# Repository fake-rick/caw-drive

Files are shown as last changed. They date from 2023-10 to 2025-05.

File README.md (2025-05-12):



# 🐦 CawDrive - 无刷电机驱动器

---



中文 | [English](https://github.com/fake-rick/caw-drive/blob/master/Docs/README_EN.md)

# 🚀 简介

- 支持 24 电压输入

- 外部编码器接口支持：霍尔，SPI，I2C

- 主控芯片：STM32F446，电机驱动芯片为 DRV8323RSRGZR

- 板载磁编码器：MT6835GT-STD（21bit）

- 支持电机线圈温度采样和驱动器温度采样

- 支持双路低端相电流采样

- 支持母线电压采样

- 支持CAN和USART通讯

- 支持SWD下载和调试

- 支持 6xPWM 和 3xPWM 的控制

# 🗂️ 目录

* Firmware：旧版代码（弃用）

* Firmware_F446：FOC控制的实际控制代码以及STM32CubeMX配置

* PCB：FOC驱动器原理图、PCB以及生成的Gerber文件

# 📦 固件编译（开发中）

## 配置caw-embedded库

当前固件编译依赖caw-embedded项目: https://github.com/fake-rick/caw-embedded

依赖添加方式1：

可以直接将caw-embedded项目克隆到caw-drive/Firmware目录下:

```bash
cd caw-drive/Firmware
git clone git@github.com:fake-rick/caw-embedded.git caw_embedded
```

依赖添加方式2：

将caw-embedded项目克隆后建立链接（Linux），假设将caw-embedded放在与caw-drive同级目录下:

```bash
git clone git@github.com:fake-rick/caw-embedded.git
cd caw-drive/Firmware
ln -s ../../caw-embedded caw_embedded
```

# 🛠 VSCode配置

安装并配置stm32-for-vscode插件

# 👻 图片展示

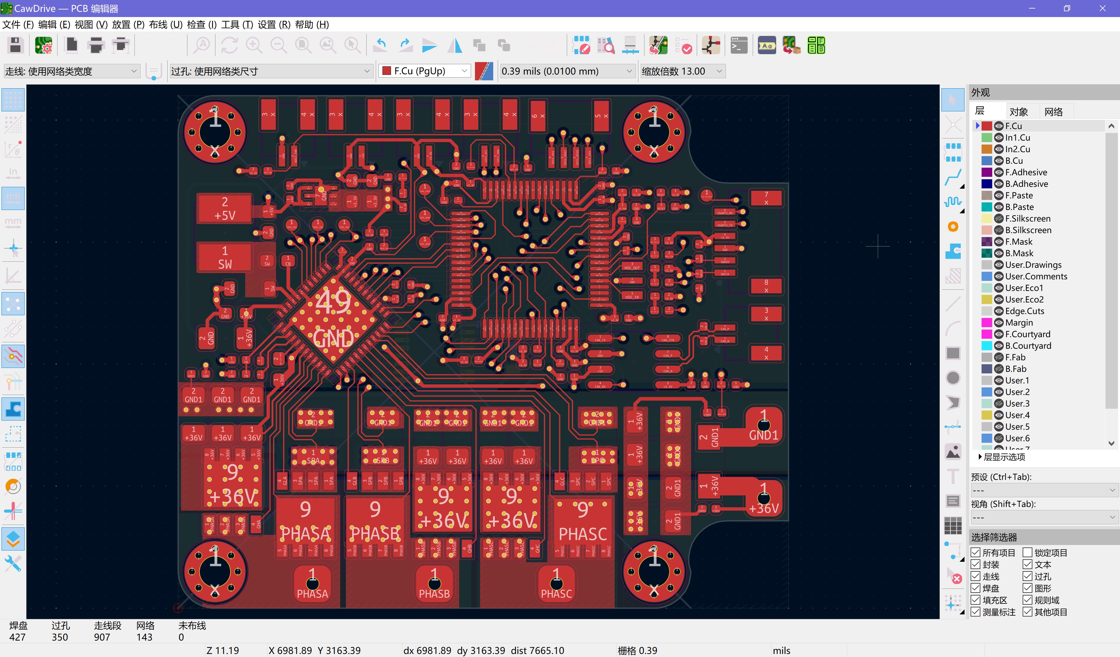
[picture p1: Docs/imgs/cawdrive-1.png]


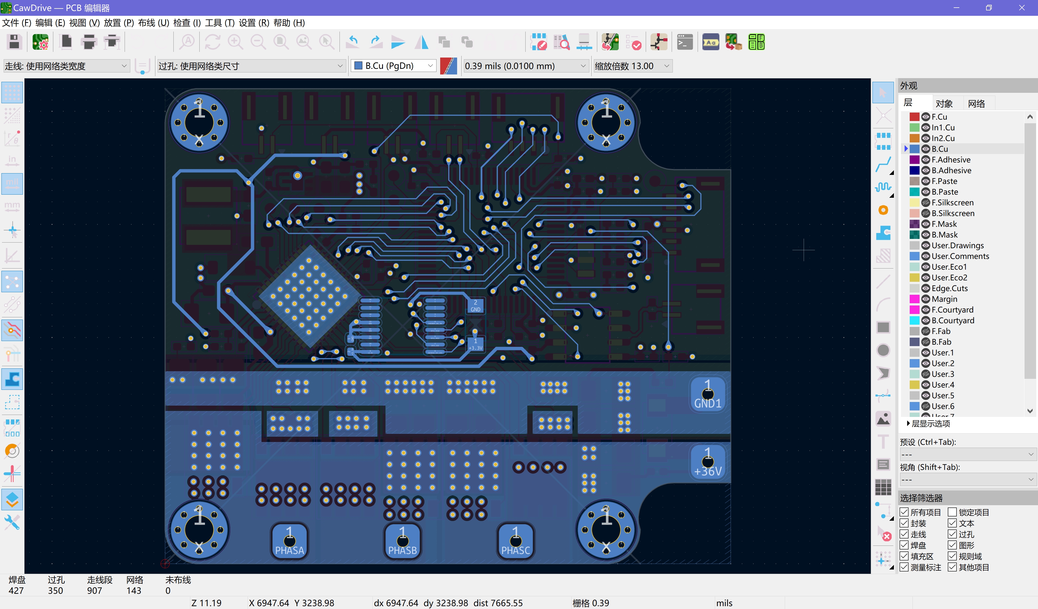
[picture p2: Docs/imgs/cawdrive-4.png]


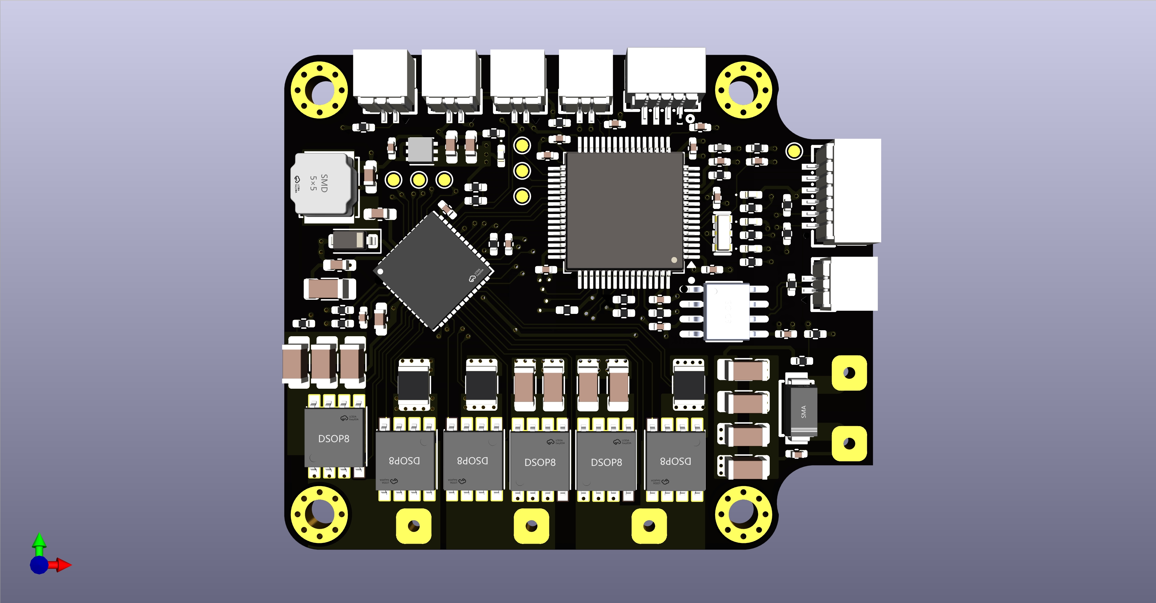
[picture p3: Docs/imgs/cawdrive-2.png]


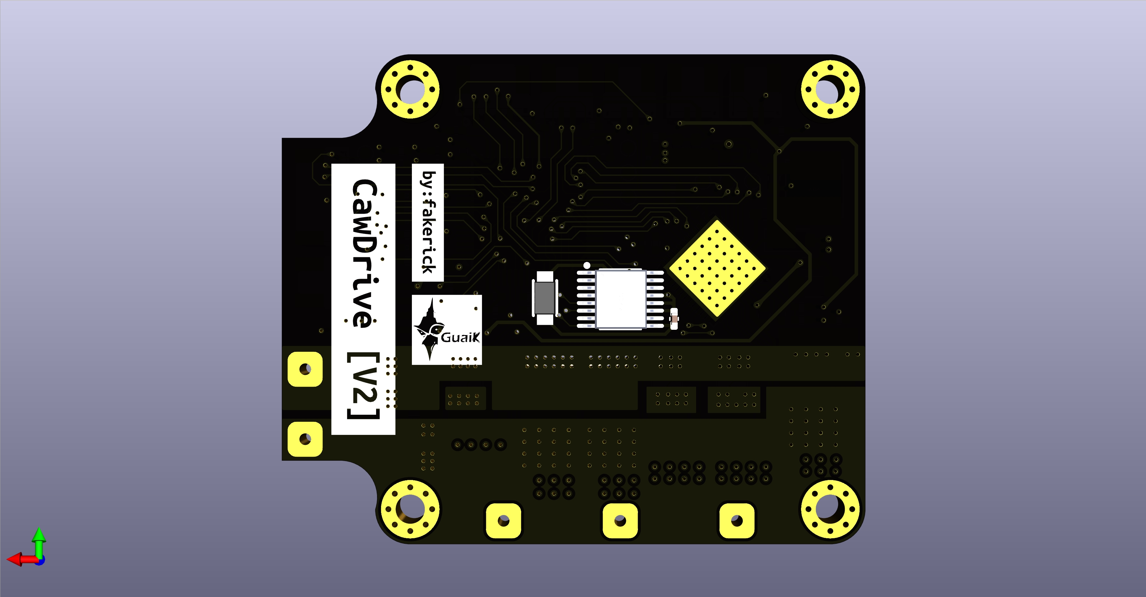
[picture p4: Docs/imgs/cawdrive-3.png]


# 🖥️ 上位机

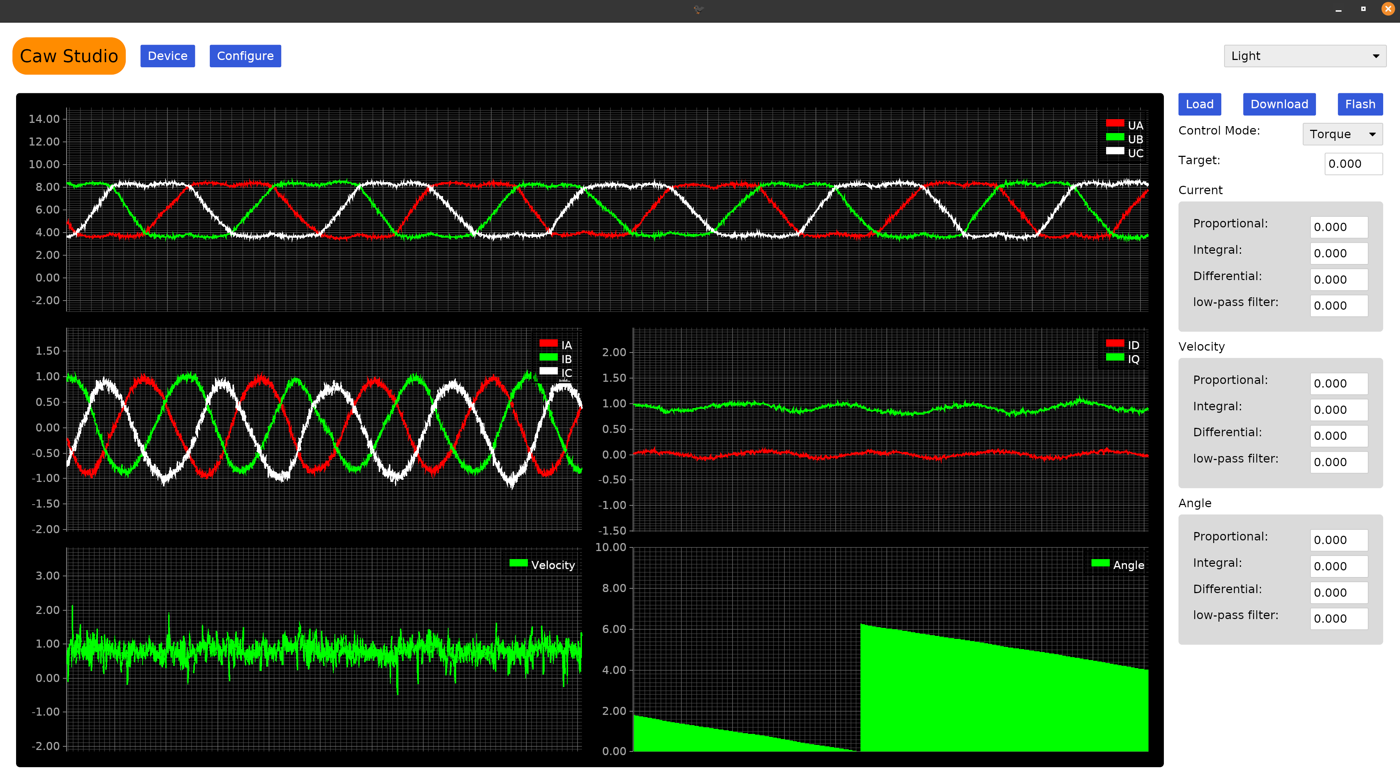
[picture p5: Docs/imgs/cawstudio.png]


# 📝 参考资料

https://github.com/bgkatz/3phase_integrated

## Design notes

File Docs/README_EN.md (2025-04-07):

# 🐦 CawDrive - Brushless Motor Driver

---



# 🚀 Introduction

- Supports 24V input

- External encoder interface support: Hall, SPI, I2C

- Main control chip: STM32F446, motor driver chip: DRV8323RSRGZR

- Onboard magnetic encoder: MT6835GT-STD (21-bit)

- Supports motor coil temperature sampling and driver temperature sampling

- Supports 3-phase low-side current sampling

- Supports bus voltage sampling

- Supports CAN and USART communication

- Supports SWD download and debugging

- Supports 6xPWM and 3xPWM control

# 🗂️ Directory

* Firmware: Legacy code (deprecated)

* Firmware_F446: Actual control code for FOC control and STM32CubeMX configuration

* PCB: FOC driver schematics, PCB, and generated Gerber files

# 📦 Firmware Compilation (Under Development)

## Configure the caw-embedded Library

The current firmware compilation depends on the caw-embedded project: https://github.com/fake-rick/caw-embedded

Dependency Addition Method 1:

You can directly clone the caw-embedded project into the `caw-drive/Firmware` directory:

```bash
cd caw-drive/Firmware
git clone git@github.com:fake-rick/caw-embedded.git caw_embedded
```

Dependency Addition Method 2:

Clone the caw-embedded project and create a symbolic link (Linux). Assuming the caw-embedded project is placed in the same level directory as caw-drive:

```bash
git clone git@github.com:fake-rick/caw-embedded.git
cd caw-drive/Firmware
ln -s ../../caw-embedded caw_embedded
```

# 🛠 VSCode Configuration

Install and configure the stm32-for-vscode plugin

# 👻 Image Showcase







# 🖥️ Upper Computer



# 📝 References

https://github.com/bgkatz/3phase_integrated

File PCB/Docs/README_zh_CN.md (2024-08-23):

# CawDrive - 无刷电机驱动器

---



# 🚀 简介

- 支持 24 电压输入

- 当前版本支持 SPI，串口和 CAN FD 总线通讯，支持 TIM PWM 刹车功能

- 主控芯片：STM32G474，电机驱动芯片为 DRV8323RSRGZR

- 板载磁编码器：AS5047P

- 支持一路NTC采样

- 支持 6xPWM 和 3xPWM 的控制

# ☕ 支持

### 💰 微信 & 支付宝：

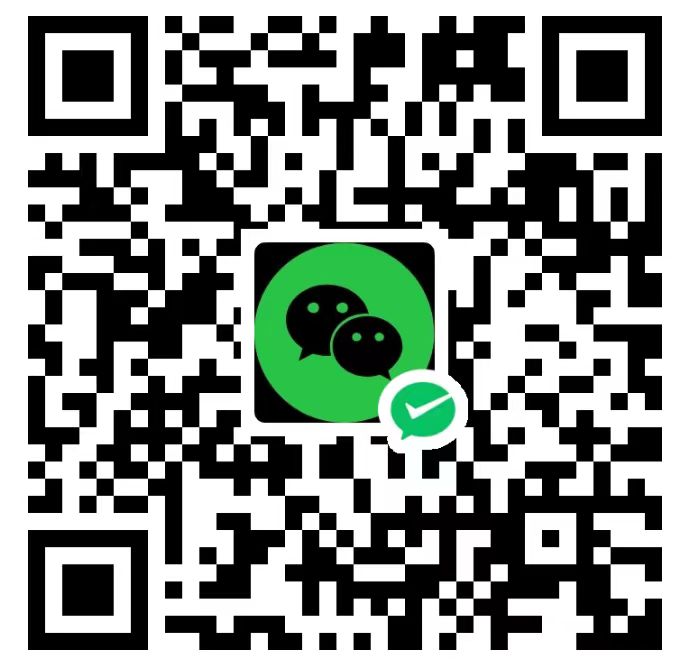
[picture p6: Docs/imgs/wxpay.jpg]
https://github.com/fake-rick/caw-drive/blob/master/Docs/imgs/wxpay.jpg?raw=true
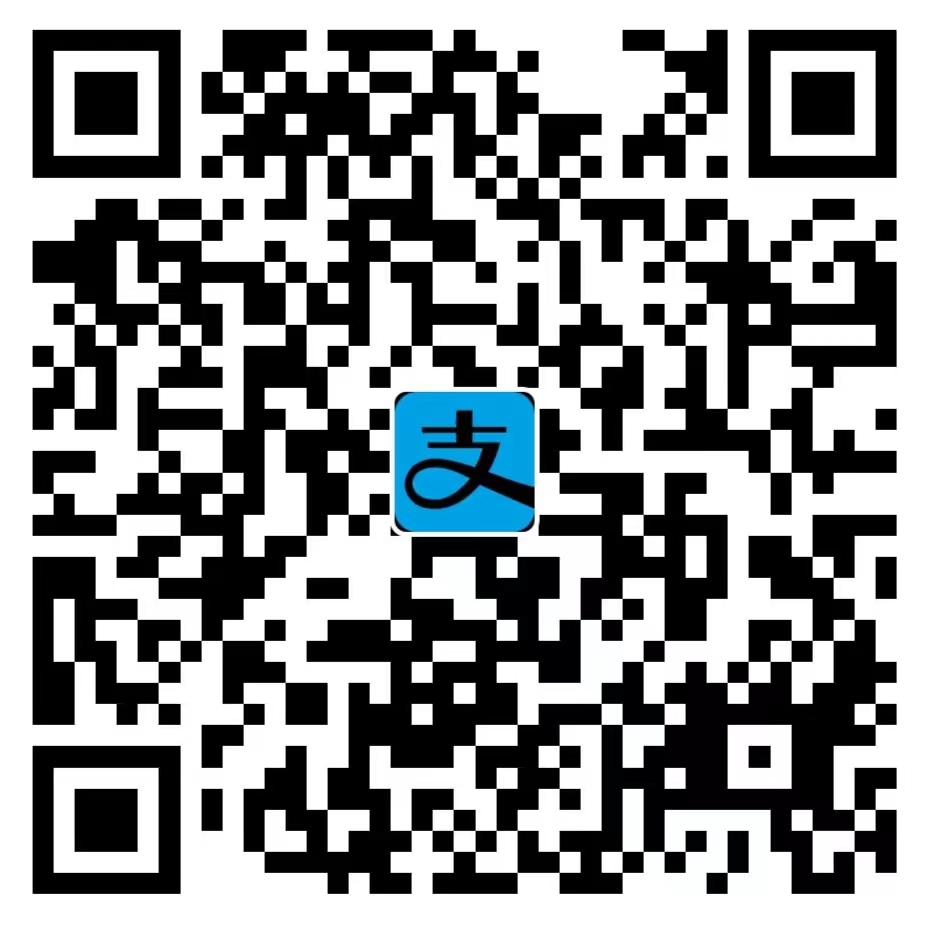
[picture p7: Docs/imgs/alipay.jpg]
https://github.com/fake-rick/caw-drive/blob/master/Docs/imgs/alipay.jpg?raw=true
 

# 📝 参考资料

[bgkatz/3phase_integrated: 3-phase motor controller with integrated position sensor (github.com)](https://github.com/bgkatz/3phase_integrated)

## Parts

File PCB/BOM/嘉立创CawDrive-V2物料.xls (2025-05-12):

购买类型 | 商品编号 | 物料编码 | 商品分类 | 名称 | 商品型号 | 品牌 | 封装规格 | 单个毛重 | 购买数量 | 商品单价(元) | 金额(元)
现货 | C87270 |  | 静电和浪涌保护(TVS/ESD) | 双向TVS 36V截止 6.9A峰值脉冲 编带 | SMAJ36CA/TR13 | Brightking(君耀电子) | SMA(DO-214AC) | 0.000122000 | 20 | 0.224 | 4.48
现货 | C3029343 |  | 线对板针座 | 1x4P 间距:1mm 卧贴 系列:SH 编带 | WAFER-SH1.0-4PWB | XUNPU(讯普) | SMD,P=1mm,卧贴 | 0.000240000 | 5 | 0.557 | 2.79
现货 | C3029345 |  | 线对板针座 | 1x6P 间距:1mm 卧贴 系列:SH 编带 | WAFER-SH1.0-6PWB | XUNPU(讯普) | SMD,P=1mm,卧贴 | 0.000270000 | 5 | 0.6758 | 3.38
现货 | C141553 |  | 场效应管(MOSFET) | 1个N沟道 耐压:40V 电流:92A 编带 | TPH3R704PL,L1Q | TOSHIBA(东芝) | DSOP-8-EP-5.0mm | 0.000107000 | 12 | 3.73 | 44.76
现货 | C69336 |  | 单片机(MCU/MPU/SOC) | MSL=3 带DSP和FPU的高性能基础系列ARM Cortex-M4 MCU，具有512 KB Flash、180 MHz CPU、ART加速器和双QSPI 托盘 | STM32F446RET6 | ST(意法半导体) | LQFP-64(10x10) | 0.001913000 | 2 | 31.65 | 63.3
现货 | C2848334 |  | 线性稳压器(LDO) | 具有可调节输出和固定输出的 1A、16V 正电压低压降 (LDO) 线性稳压器 编带 | TLV76733DRVR | TI(德州仪器) | WSON-6(2x2) | 0.000190000 | 5 | 1.2651 | 6.33
现货 | C38695 |  | CAN收发器 | TJA1051T/3/1J 编带 | TJA1051T/3/1J | NXP(恩智浦) | SOIC-8-150mil | 0.000193000 | 5 | 3.4 | 17
现货 | C3029341 |  | 线对板针座 | 1x2P 间距:1mm 卧贴 系列:SH 编带 | WAFER-SH1.0-2PWB | XUNPU(讯普) | SMD,P=1mm,卧贴 | 0.000200000 | 10 | 0.4252 | 4.25
现货 | C82544 |  | 肖特基二极管 | 电压:40V 电流:1A 编带 | 1N5819HW-7-F | DIODES(美台) | SOD-123 | 0.000035000 | 20 | 0.1823 | 3.65
现货 | C86063 |  | 贴片电感 | 39nH ±5% 编带 | LQG15HS39NJ02D | muRata(村田) | 0402 | 0.000015000 | 100 | 0.0465 | 4.65
现货 | C965790 |  | 发光二极管/LED | 停产 XL-1005SURC 编带 | XL-1005SURC | XINGLIGHT(成兴光) | 0402 | 0.000022000 | 100 | 0.0497 | 4.97
现货 | C22355736 |  | 发光二极管/LED | XL-1005UBC 编带 | XL-1005UBC | XINGLIGHT(成兴光) | 0402 | 0.000016040 | 100 | 0.0471 | 4.71
现货 | C965793 |  | 发光二极管/LED | XL-1005UGC 编带 | XL-1005UGC | XINGLIGHT(成兴光) | 0402 | 0.000022000 | 100 | 0.0478 | 4.78
现货 | C965791 |  | 发光二极管/LED | XL-1005UOC 编带 | XL-1005UOC | XINGLIGHT(成兴光) | 0402 | 0.000022000 | 50 | 0.0767 | 3.84
现货 | C167941 |  | 功率电感 | 22uH ±20% 1.2A 编带 | FNR5020S220MT | cjiang(长江微电) | SMD,5x5mm | 0.000181000 | 10 | 0.379 | 3.79
现货 | C25079 |  | 贴片电阻 | 120Ω ±1% 62.5mW 厚膜电阻 编带 | 0402WGF1200TCE | UNI-ROYAL(厚声) | 0402 | 0.000009000 | 100 | 0.0038 | 0.38
现货 | C77131 |  | NTC热敏电阻 | NCP15XH103F03RC 编带 | NCP15XH103F03RC | muRata(村田) | 0402 | 0.000015000 | 50 | 0.0674 | 3.37
现货 | C852841 |  | 贴片电阻 | 薄膜电阻 54.9kΩ ±0.1% 62.5mW 编带 | RT0402BRD0754K9L | YAGEO(国巨) | 0402 | 0.000009000 | 50 | 0.1335 | 6.68
现货 | C281777 |  | 贴片电阻 | 薄膜电阻 3kΩ ±0.1% 62.5mW 编带 | RT0402BRD073KL | YAGEO(国巨) | 0402 | 0.000009000 | 50 | 0.1253 | 6.27
现货 | C728563 |  | 贴片电阻 | 薄膜电阻 75kΩ ±0.1% 62.5mW 编带 | RT0402BRD0775KL | YAGEO(国巨) | 0402 | 0.000009000 | 50 | 0.1294 | 6.47
现货 | C2988648 |  | 电流采样电阻/分流器 | 5mΩ ±1% 1W 编带 | HoLLR1206-1W-5mR-1% | Milliohm(毫欧) | 1206 | 0.000032000 | 10 | 0.3007 | 3.01
现货 | C17168 |  | 贴片电阻 | 0Ω ±1% 62.5mW 厚膜电阻 编带 | 0402WGF0000TCE | UNI-ROYAL(厚声) | 0402 | 0.000009000 | 100 | 0.0033 | 0.33
现货 | C190095 |  | 贴片电阻 | 薄膜电阻 10kΩ ±0.1% 62.5mW 编带 | RT0402BRD0710KL | YAGEO(国巨) | 0402 | 0.000009000 | 50 | 0.1107 | 5.54
现货 | C25123 |  | 贴片电阻 | 510Ω ±1% 62.5mW 厚膜电阻 编带 | 0402WGF5100TCE | UNI-ROYAL(厚声) | 0402 | 0.000009000 | 100 | 0.0035 | 0.35
现货 | C25744 |  | 贴片电阻 | 10kΩ ±1% 62.5mW 厚膜电阻 编带 | 0402WGF1002TCE | UNI-ROYAL(厚声) | 0402 | 0.000010178 | 100 | 0.0034 | 0.34
现货 | C24497 |  | 贴片电容(MLCC) | 100nF ±10% 50V 编带 | CL31B104KBCNNNC | SAMSUNG(三星) | 1206 | 0.000074000 | 20 | 0.0948 | 1.9
现货 | C15849 |  | 贴片电容(MLCC) | 1uF ±10% 50V 编带 | CL10A105KB8NNNC | SAMSUNG(三星) | 0603 | 0.000042321 | 50 | 0.0336 | 1.68
现货 | C272875 |  | 贴片电容(MLCC) | 47nF ±10% 50V 编带 | CC0402KRX7R9BB473 | YAGEO(国巨) | 0402 | 0.000009000 | 100 | 0.0147 | 1.47
现货 | C107369 |  | 贴片电容(MLCC) | 2.2uF ±10% 10V 编带 | CL05A225KP5NSNC | SAMSUNG(三星) | 0402 | 0.000013000 | 100 | 0.0221 | 2.21
现货 | C1591 |  | 贴片电容(MLCC) | 100nF ±10% 50V 编带 | CL10B104KB8NNNC | SAMSUNG(三星) | 0603 | 0.000045000 | 100 | 0.0176 | 1.76
现货 | C77020 |  | 贴片电容(MLCC) | 100nF ±10% 50V 编带 | GRM155R71H104KE14D | muRata(村田) | 0402 | 0.000012000 | 100 | 0.0205 | 2.05
现货 | C86295 |  | 贴片电容(MLCC) | 22uF ±20% 10V 编带 | CL10A226MP8NUNE | SAMSUNG(三星) | 0603 | 0.000045000 | 30 | 0.0959 | 2.88
现货 | C14445 |  | 贴片电容(MLCC) | 1uF ±10% 10V 编带 | CL05A105KP5NNNC | SAMSUNG(三星) | 0402 | 0.000016500 | 100 | 0.0123 | 1.23
现货 | C13585 |  | 贴片电容(MLCC) | 10uF ±10% 50V 编带 | CL31A106KBHNNNE | SAMSUNG(三星) | 1206 | 0.000082900 | 30 | 0.2244 | 6.73
现货 | C60474 |  | 贴片电容(MLCC) | 100nF ±10% 16V 编带 | CC0402KRX7R7BB104 | YAGEO(国巨) | 0402 | 0.000013670 | 100 | 0.0057 | 0.57

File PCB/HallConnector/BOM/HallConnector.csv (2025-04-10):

Source: | E:\Workspace\caw\CawDrive\PCB\HallConnector\HallConnector.kicad_sch
Date: | 2025-04-10T22:04:38+0800
Tool: | Eeschema 9.0.1
Generator: | C:\Program Files\KiCad\9.0\bin\scripting\plugins/bom_csv_grouped_by_value.py
Component Count: | 13
Collated Components:
Item | Qty | Reference(s) | Value | LibPart | Footprint | Datasheet | DNP | Datasheet | Description | Footprint | SuppliersPartNumber | uuid
1 | 3 | C1, C2, C3 | 10pF | Device:C_Small | Capacitor_SMD:C_0603_1608Metric_Pad1.08x0.95mm_HandSolder | ~ |  | ~ | Unpolarized capacitor, small symbol | Capacitor_SMD:C_0603_1608Metric_Pad1.08x0.95mm_HandSolder
2 | 1 | CN3 | WAFER-SH1.0-4PWB | Rick_Connector:WAFER-SH1.0-4PWB | Rick_Connector:CONN-SMD_4P-P1.00_WAFER-SH1.0-4PWB |  |  |  |  | Rick_Connector:CONN-SMD_4P-P1.00_WAFER-SH1.0-4PWB | C3029343 | std:3aeef2007f6340e5aa158e9b3ba53384
3 | 1 | J1 | Conn_01x05_Pin | Connector:Conn_01x05_Pin | Connector_PinHeader_2.54mm:PinHeader_1x05_P2.54mm_Vertical | ~ |  | ~ | Generic connector, single row, 01x05, script generated | Connector_PinHeader_2.54mm:PinHeader_1x05_P2.54mm_Vertical
4 | 3 | R1, R2, R3 | 10k | Device:R_Small_US | Resistor_SMD:R_0603_1608Metric_Pad0.98x0.95mm_HandSolder | ~ |  | ~ | Resistor, small US symbol | Resistor_SMD:R_0603_1608Metric_Pad0.98x0.95mm_HandSolder
5 | 3 | R4, R5, R6 | 1.8k | Device:R_Small_US | Resistor_SMD:R_0603_1608Metric_Pad0.98x0.95mm_HandSolder | ~ |  | ~ | Resistor, small US symbol | Resistor_SMD:R_0603_1608Metric_Pad0.98x0.95mm_HandSolder
6 | 2 | U1, U2 | WAFER-SH1.0-2PWB | Rick_Connector:WAFER-SH1.0-2PWB | Rick_Connector:CONN-SMD_2P-P1.00_XUNPU_WAFER-SH1.0-2PWB |  |  |  |  | Rick_Connector:CONN-SMD_2P-P1.00_XUNPU_WAFER-SH1.0-2PWB | C3029341 | std:b25617d4d4944bb5a333c9a533c58e4a

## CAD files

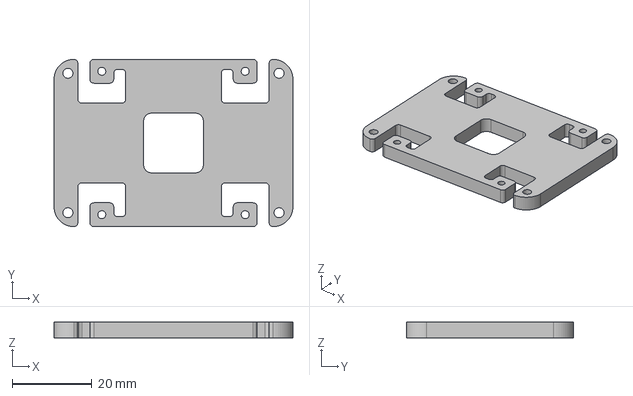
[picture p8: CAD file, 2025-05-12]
Docs/CawDrive-Fixed v1.step
60.0 x 42.0 x 4.00 mm

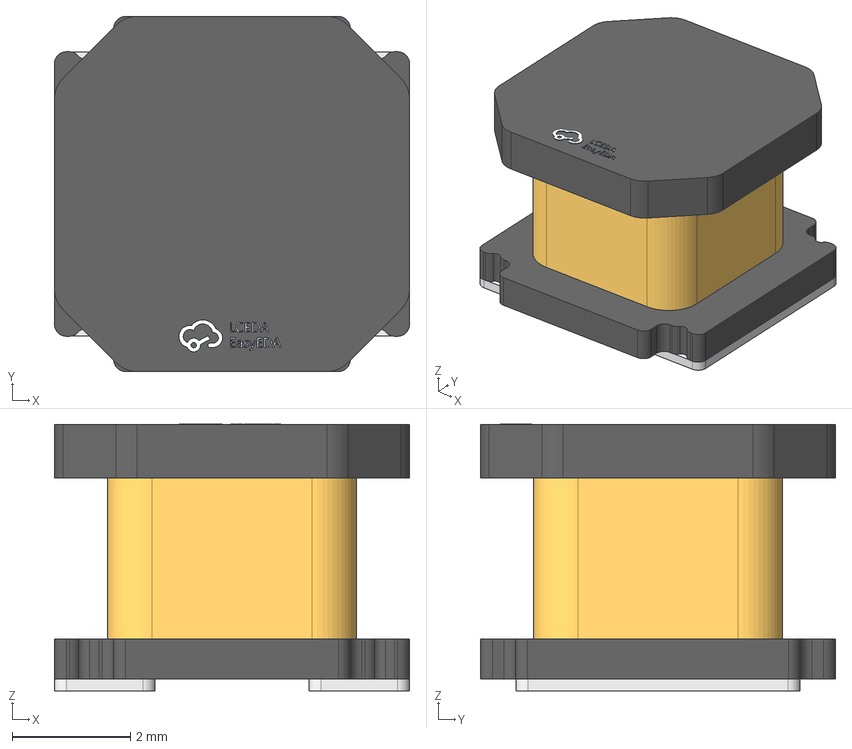
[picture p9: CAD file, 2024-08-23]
PCB/3DModel/VLS6045EX-220M.step
6.00 x 6.00 x 4.51 mm

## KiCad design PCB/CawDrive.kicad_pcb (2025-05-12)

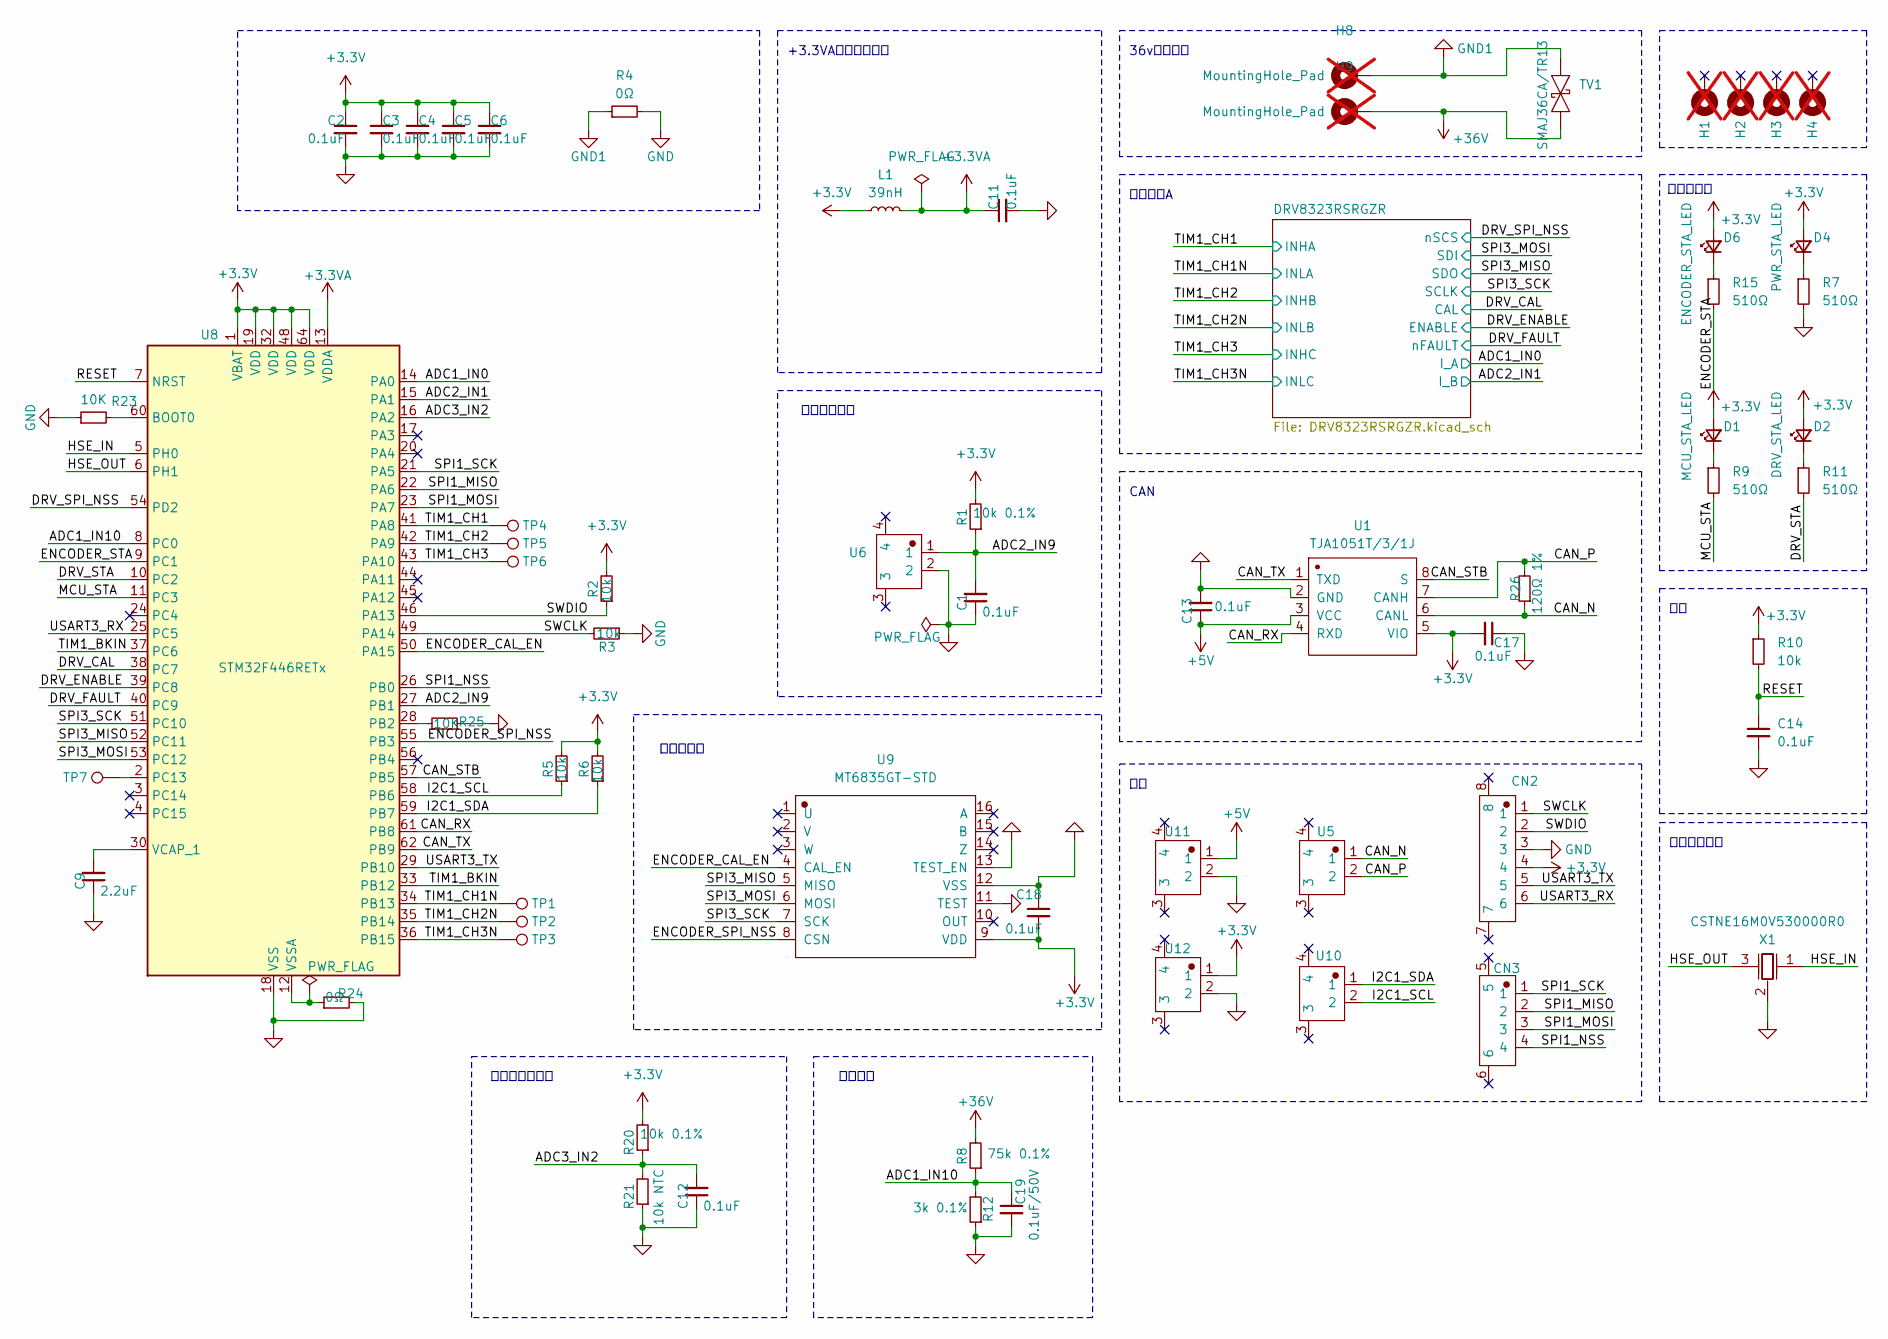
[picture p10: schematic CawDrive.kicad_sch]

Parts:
C1, C2, C3, C4, C5, C6, C11, C12, C13, C14, C17, C18: 0.1uF; C_0402_1005Metric_Pad0.74x0.62mm_HandSolder
C9: 2.2uF; C_0402_1005Metric_Pad0.74x0.62mm_HandSolder
C19: 0.1uF/50V; C_0402_1005Metric_Pad0.74x0.62mm_HandSolder
CN2: WAFER-SH1.0-6PWB; CONN-SMD_6P-P1.00_XUNPU_WAFER-SH1.0-6PWB
CN3: WAFER-SH1.0-4PWB; CONN-SMD_4P-P1.00_WAFER-SH1.0-4PWB
D1: MCU_STA_LED; LED_0402_1005Metric_Pad0.77x0.64mm_HandSolder
D2: DRV_STA_LED; LED_0402_1005Metric_Pad0.77x0.64mm_HandSolder
D4: PWR_STA_LED; LED_0402_1005Metric_Pad0.77x0.64mm_HandSolder
D6: ENCODER_STA_LED; LED_0402_1005Metric_Pad0.77x0.64mm_HandSolder
H1, H2, H3, H4: MountingHole_Pad; MountingHole_2.5mm_Pad_Via; not fitted
H8, H9: MountingHole_Pad; POWER_PAD; not fitted
L1: 39nH; L_0402_1005Metric_Pad0.77x0.64mm_HandSolder
R1, R20: 10k 0.1%; R_0402_1005Metric_Pad0.72x0.64mm_HandSolder
R2, R3, R5, R6, R10: 10k; R_0402_1005Metric_Pad0.72x0.64mm_HandSolder
R4, R24: 0Ω; R_0402_1005Metric_Pad0.72x0.64mm_HandSolder
R7, R9, R11, R15: 510Ω; R_0402_1005Metric_Pad0.72x0.64mm_HandSolder
R8: 75k 0.1%; R_0402_1005Metric_Pad0.72x0.64mm_HandSolder
R12: 3k 0.1%; R_0402_1005Metric_Pad0.72x0.64mm_HandSolder
R21: 10k NTC; R_0402_1005Metric_Pad0.72x0.64mm_HandSolder
R23, R25: 10K; R_0402_1005Metric_Pad0.72x0.64mm_HandSolder
R26: 120Ω 1%; R_0402_1005Metric_Pad0.72x0.64mm_HandSolder
TP1, TP2, TP3, TP4, TP5, TP6, TP7: TestPoint; TestPoint_Pad_D1.0mm
TV1: SMAJ36CA/TR13; SMAJ36CA_TR13_SMA(DO-214AC); JLC Part Number C87270
U1: TJA1051T/3/1J; TJA1051T31J_SOIC-8_L4.9-W3.9-P1.27-LS6.0-BL
U5, U6, U10, U11, U12: WAFER-SH1.0-2PWB; CONN-SMD_2P-P1.00_XUNPU_WAFER-SH1.0-2PWB
U8: STM32F446RETx; LQFP-64_10x10mm_P0.5mm
U9: MT6835GT-STD
X1: CSTNE16M0V530000R0; Crystal_SMD3213-3P; JLC Part Number C341521

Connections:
+3.3V: C2.1, C3.1, C4.1, C5.1, C6.1, C17.2, C18.2, CN2.4, D1.2 (A), D2.2 (A), D4.2 (A), D6.2 (A), L1.1, R1.2, R2.2, R5.2, R6.2, R10.1, R20.2, U1.5 (VIO), U8.1 (VBAT), U8.19 (VDD), U8.32 (VDD), U8.48 (VDD), U8.64 (VDD), U9.9 (VDD), U12.1; also elsewhere on the board
+3.3VA: C11.1, L1.2, U8.13 (VDDA)
+5V: C13.1, U1.3 (VCC), U11.1; also elsewhere on the board
+36V: H9.1, R8.2, TV1.1 (K); also elsewhere on the board
/ADC1_IN0: U8.14 (PA0); also elsewhere on the board
/ADC1_IN10: C19.1, R8.1, R12.2, U8.8 (PC0)
/ADC2_IN1: U8.15 (PA1); also elsewhere on the board
/ADC2_IN9: C1.2, R1.1, U6.1, U8.27 (PB1)
/ADC3_IN2: C12.2, R20.1, R21.2, U8.16 (PA2)
/CAN_N: R26.1, U1.6 (CANL), U5.1
/CAN_P: R26.2, U1.7 (CANH), U5.2
/CAN_RX: U1.4 (RXD), U8.61 (PB8)
/CAN_STB: U1.8 (S), U8.57 (PB5)
/CAN_TX: U1.1 (TXD), U8.62 (PB9)
/DRV_CAL: U8.38 (PC7); also elsewhere on the board
/DRV_ENABLE: U8.39 (PC8); also elsewhere on the board
/DRV_FAULT: U8.40 (PC9); also elsewhere on the board
/DRV_SPI_NSS: U8.54 (PD2); also elsewhere on the board
/DRV_STA: R11.2, U8.10 (PC2)
/ENCODER_CAL_EN: U8.50 (PA15), U9.4 (CAL_EN)
/ENCODER_SPI_NSS: U8.55 (PB3), U9.8 (CSN)
/ENCODER_STA: R15.2, U8.9 (PC1)
/HSE_IN: U8.5 (PH0), X1.1 (OSC1)
/HSE_OUT: U8.6 (PH1), X1.3 (OSC2)
/I2C1_SCL: R5.1, U8.58 (PB6), U10.2
/I2C1_SDA: R6.1, U8.59 (PB7), U10.1
/MCU_STA: R9.2, U8.11 (PC3)
/RESET: C14.1, R10.2, U8.7 (NRST)
/SPI1_MISO: CN3.2, U8.22 (PA6)
/SPI1_MOSI: CN3.3, U8.23 (PA7)
/SPI1_NSS: CN3.4, U8.26 (PB0)
/SPI1_SCK: CN3.1, U8.21 (PA5)
/SPI3_MISO: U8.52 (PC11), U9.5 (MISO); also elsewhere on the board
/SPI3_MOSI: U8.53 (PC12), U9.6 (MOSI); also elsewhere on the board
/SPI3_SCK: U8.51 (PC10), U9.7 (SCK); also elsewhere on the board
/SWCLK: CN2.1, R3.2, U8.49 (PA14)
/SWDIO: CN2.2, R2.1, U8.46 (PA13)
/TIM1_BKIN: U8.33 (PB12), U8.37 (PC6)
/TIM1_CH1: TP4.1, U8.41 (PA8); also elsewhere on the board
/TIM1_CH1N: TP1.1, U8.34 (PB13); also elsewhere on the board
/TIM1_CH2: TP5.1, U8.42 (PA9); also elsewhere on the board
/TIM1_CH2N: TP2.1, U8.35 (PB14); also elsewhere on the board
/TIM1_CH3: TP6.1, U8.43 (PA10); also elsewhere on the board
/TIM1_CH3N: TP3.1, U8.36 (PB15); also elsewhere on the board
/USART3_RX: CN2.6, U8.25 (PC5)
/USART3_TX: CN2.5, U8.29 (PB10)
GND: C1.1, C2.2, C3.2, C4.2, C5.2, C6.2, C9.1, C11.2, C12.1, C13.2, C14.2, C17.1, C18.1, C19.2, CN2.3, R3.1, R4.2, R7.2, R12.1, R21.1, R23.1, R24.2, R25.2, U1.2 (GND), U6.2, U8.18 (VSS), U8.31 (VSS), U8.47 (VSS), U8.63 (VSS), U9.11 (TEST), U9.12 (VSS), U9.13 (TEST_EN), U11.2, U12.2, X1.2 (GND); also elsewhere on the board
GND1: H8.1, R4.1, TV1.2 (A); also elsewhere on the board
unnamed: D1.1 (K), R9.1
unnamed: D2.1 (K), R11.1
unnamed: D4.1 (K), R7.1
unnamed: D6.1 (K), R15.1
unnamed: R23.2, U8.60 (BOOT0)
unnamed: R25.1, U8.28 (PB2)
unnamed: TP7.1, U8.2 (PC13)
unnamed: C9.2, U8.30 (VCAP_1)
unnamed: R24.1, U8.12 (VSSA)

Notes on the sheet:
母线电压
电机温度采样
驱动器温度采样
36v电源输入
CAN
+3.3VA模拟电源滤波
位置传感器
电机驱动A
外部高速晶振
状态指示灯

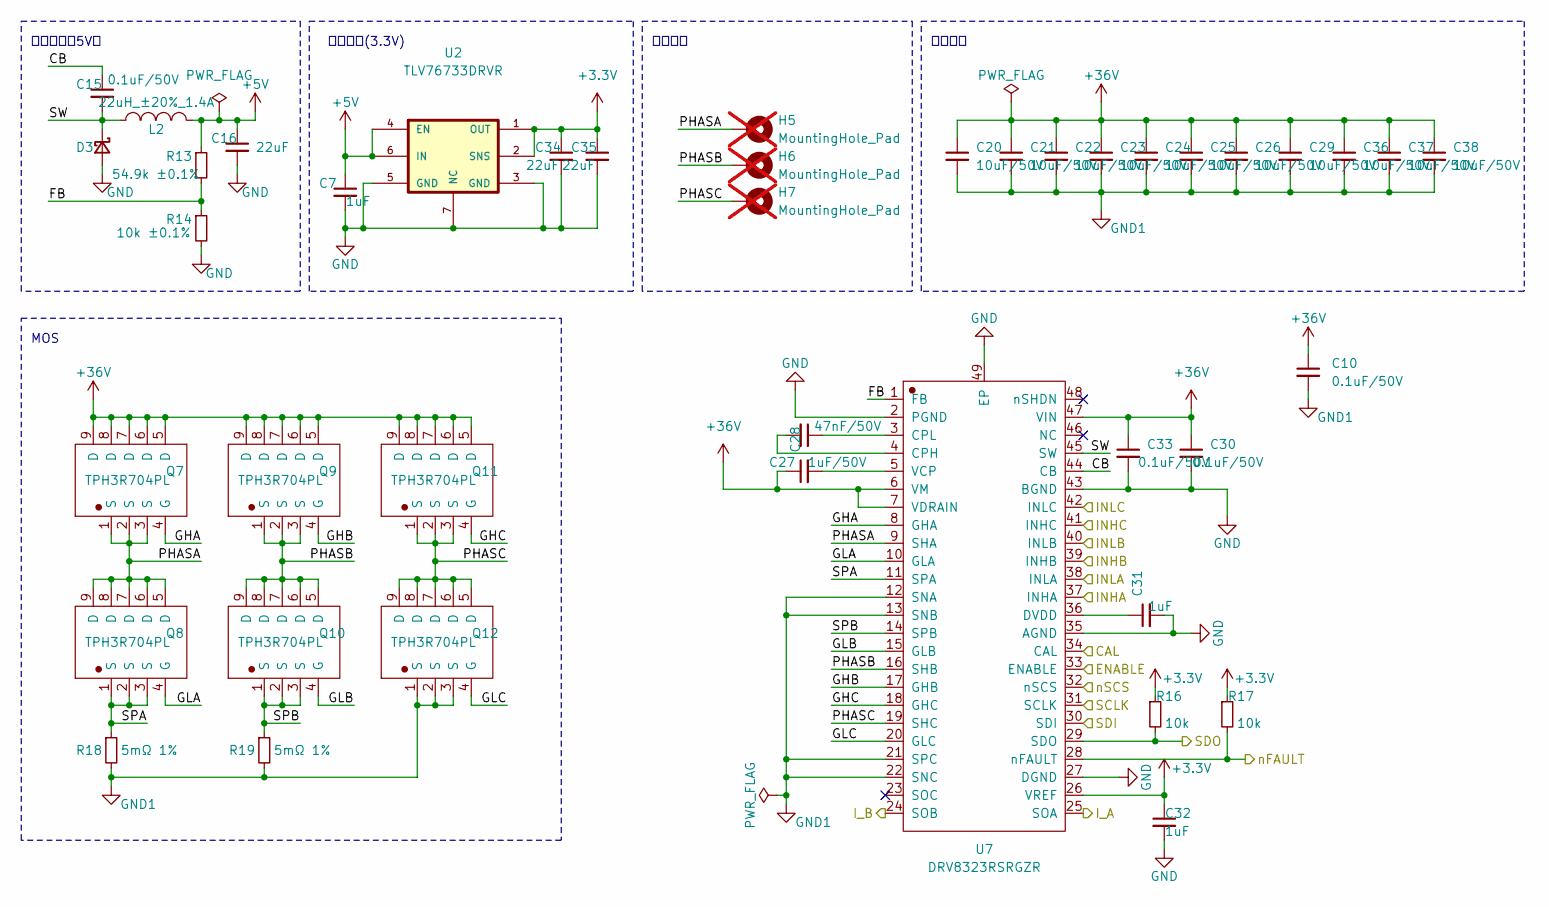
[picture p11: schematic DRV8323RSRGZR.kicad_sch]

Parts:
C7, C31, C32: 1uF; C_0402_1005Metric_Pad0.74x0.62mm_HandSolder
C10: 0.1uF/50V; C_0402_1005Metric_Pad0.74x0.62mm_HandSolder
C15, C33: 0.1uF/50V; C_0603_1608Metric_Pad1.08x0.95mm_HandSolder
C16, C34, C35: 22uF; C_0603_1608Metric_Pad1.08x0.95mm_HandSolder
C20, C21, C22, C23, C24, C25, C26, C29, C36, C37, C38: 10uF/50V; C_1206_3216Metric_Pad1.33x1.80mm_HandSolder
C27: 47nF/50V; C_0402_1005Metric_Pad0.74x0.62mm_HandSolder
C28: 1uF/50V; C_0603_1608Metric_Pad1.08x0.95mm_HandSolder
C30: 0.1uF/50V; C_1206_3216Metric_Pad1.33x1.80mm_HandSolder
D3: D_Schottky_Small; D_SOD-123
H5, H6, H7: MountingHole_Pad; POWER_PAD; not fitted
L2: 22uH_±20%_1.4A; LQH5BPB220MT0L_IND-SMD_L5.0-W5.0
Q7, Q8, Q9, Q10, Q11, Q12: TPH3R704PL; TPHR8504PL,L1Q
R13: 54.9k ±0.1%; R_0402_1005Metric_Pad0.72x0.64mm_HandSolder
R14: 10k ±0.1%; R_0402_1005Metric_Pad0.72x0.64mm_HandSolder
R16, R17: 10k; R_0402_1005Metric_Pad0.72x0.64mm_HandSolder
R18, R19: 5mΩ 1%; R_1210_3225Metric_Pad1.30x2.65mm_HandSolder
U2: TLV76733DRVR; TLV76733DRVR_SON65P200X200X80-7N
U7: DRV8323RSRGZR; DRV8323RS_QFN-48-EP(7x7); JLC Part Number C545497

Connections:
+3.3V: C32.1, C34.1, C35.1, R16.1, R17.1, U2.1 (OUT), U2.2 (SNS), U7.26 (VREF); also elsewhere on the board
+5V: C7.1, C16.1, L2.2, R13.1, U2.4 (EN), U2.6 (IN); also elsewhere on the board
+36V: C10.1, C20.1, C21.1, C22.1, C23.1, C24.1, C25.1, C26.1, C28.1, C29.1, C30.1, C33.1, C36.1, C37.1, C38.1, Q7.5 (D), Q7.6 (D), Q7.7 (D), Q7.8 (D), Q7.9 (D), Q9.5 (D), Q9.6 (D), Q9.7 (D), Q9.8 (D), Q9.9 (D), Q11.5 (D), Q11.6 (D), Q11.7 (D), Q11.8 (D), Q11.9 (D), U7.6 (VM), U7.7 (VDRAIN), U7.47 (VIN); also elsewhere on the board
/ADC1_IN0: U7.25 (SOA); also elsewhere on the board
/ADC2_IN1: U7.24 (SOB); also elsewhere on the board
/DRV8323RSRGZR/CB: C15.1, U7.44 (CB)
/DRV8323RSRGZR/FB: R13.2, R14.1, U7.1 (FB)
/DRV8323RSRGZR/GHA: Q7.4 (G), U7.8 (GHA)
/DRV8323RSRGZR/GHB: Q9.4 (G), U7.17 (GHB)
/DRV8323RSRGZR/GHC: Q11.4 (G), U7.18 (GHC)
/DRV8323RSRGZR/GLA: Q8.4 (G), U7.10 (GLA)
/DRV8323RSRGZR/GLB: Q10.4 (G), U7.15 (GLB)
/DRV8323RSRGZR/GLC: Q12.4 (G), U7.20 (GLC)
/DRV8323RSRGZR/PHASA: H5.1, Q7.1 (S), Q7.2 (S), Q7.3 (S), Q8.5 (D), Q8.6 (D), Q8.7 (D), Q8.8 (D), Q8.9 (D), U7.9 (SHA)
/DRV8323RSRGZR/PHASB: H6.1, Q9.1 (S), Q9.2 (S), Q9.3 (S), Q10.5 (D), Q10.6 (D), Q10.7 (D), Q10.8 (D), Q10.9 (D), U7.16 (SHB)
/DRV8323RSRGZR/PHASC: H7.1, Q11.1 (S), Q11.2 (S), Q11.3 (S), Q12.5 (D), Q12.6 (D), Q12.7 (D), Q12.8 (D), Q12.9 (D), U7.19 (SHC)
/DRV8323RSRGZR/SPA: Q8.1 (S), Q8.2 (S), Q8.3 (S), R18.1, U7.11 (SPA)
/DRV8323RSRGZR/SPB: Q10.1 (S), Q10.2 (S), Q10.3 (S), R19.1, U7.14 (SPB)
/DRV8323RSRGZR/SW: C15.2, D3.1 (K), L2.1, U7.45 (SW)
/DRV_CAL: U7.34 (CAL); also elsewhere on the board
/DRV_ENABLE: U7.33 (ENABLE); also elsewhere on the board
/DRV_FAULT: R17.2, U7.28 (nFAULT); also elsewhere on the board
/DRV_SPI_NSS: U7.32 (nSCS); also elsewhere on the board
/SPI3_MISO: R16.2, U7.29 (SDO); also elsewhere on the board
/SPI3_MOSI: U7.30 (SDI); also elsewhere on the board
/SPI3_SCK: U7.31 (SCLK); also elsewhere on the board
/TIM1_CH1: U7.37 (INHA); also elsewhere on the board
/TIM1_CH1N: U7.38 (INLA); also elsewhere on the board
/TIM1_CH2: U7.39 (INHB); also elsewhere on the board
/TIM1_CH2N: U7.40 (INLB); also elsewhere on the board
/TIM1_CH3: U7.41 (INHC); also elsewhere on the board
/TIM1_CH3N: U7.42 (INLC); also elsewhere on the board
GND: C7.2, C16.2, C30.2, C31.2, C32.2, C33.2, C34.2, C35.2, D3.2 (A), R14.2, U2.3 (GND), U2.5 (GND), U2.7 (NC), U7.2 (PGND), U7.27 (DGND), U7.35 (AGND), U7.43 (BGND), U7.49 (EP); also elsewhere on the board
GND1: C10.2, C20.2, C21.2, C22.2, C23.2, C24.2, C25.2, C26.2, C29.2, C36.2, C37.2, C38.2, Q12.1 (S), Q12.2 (S), Q12.3 (S), R18.2, R19.2, U7.12 (SNA), U7.13 (SNB), U7.21 (SPC), U7.22 (SNC); also elsewhere on the board
unnamed: C27.2, U7.4 (CPH)
unnamed: C27.1, U7.3 (CPL)
unnamed: C31.1, U7.36 (DVDD)
unnamed: C28.2, U7.5 (VCP)

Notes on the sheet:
滤波电容
降压电路(3.3V)
电机接口
降压电路（5V）
MOS

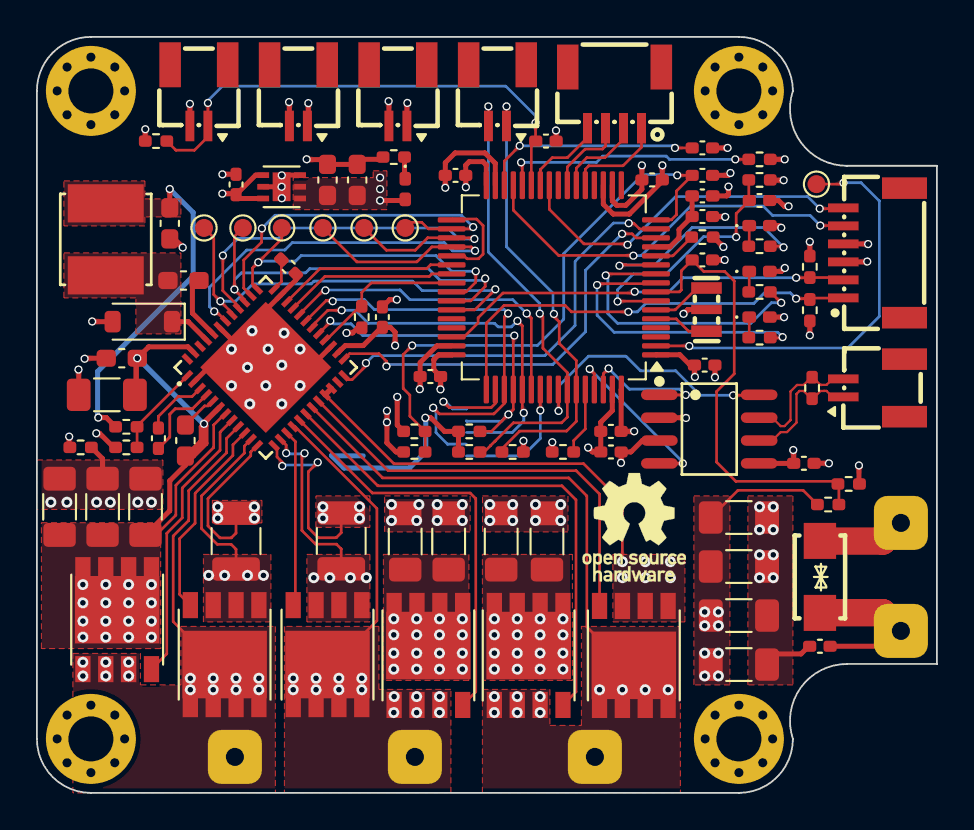
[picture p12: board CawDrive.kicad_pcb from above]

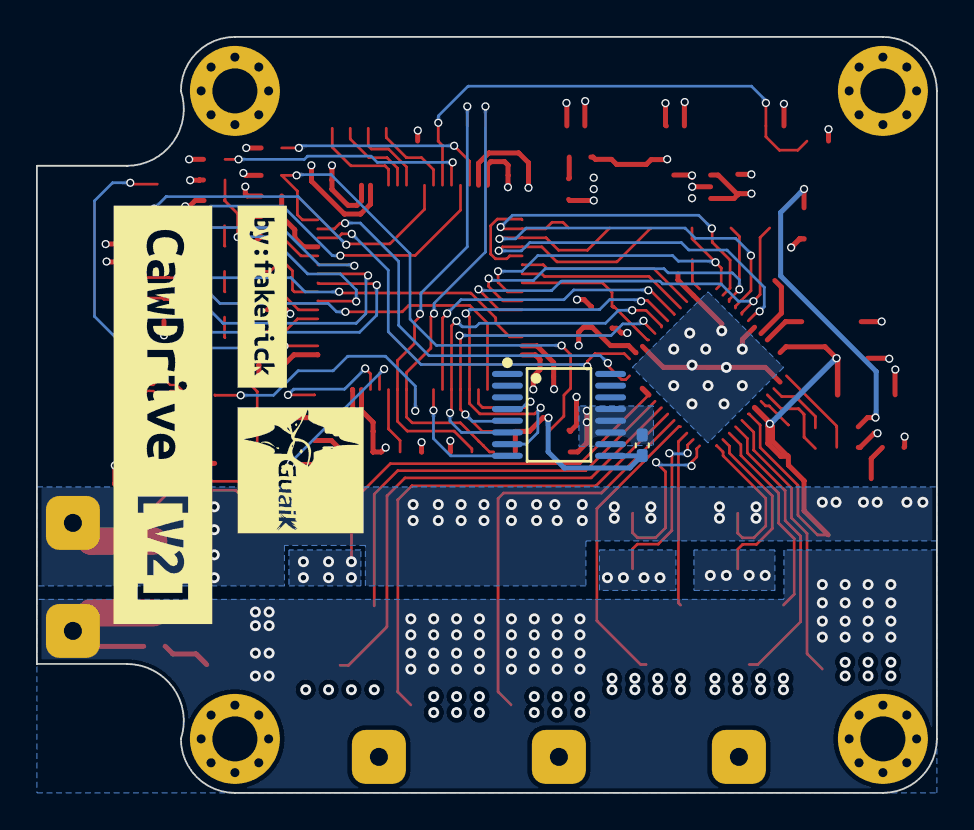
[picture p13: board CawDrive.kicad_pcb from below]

Board: 4 copper layers, 50.0 x 42.0 mm, 107 parts (4 on the bottom side), 75 nets.

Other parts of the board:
kibuzzard-67F13BB6: G***; kibuzzard-67F13BB6
kibuzzard-67F4292F: G***; kibuzzard-67F4292F

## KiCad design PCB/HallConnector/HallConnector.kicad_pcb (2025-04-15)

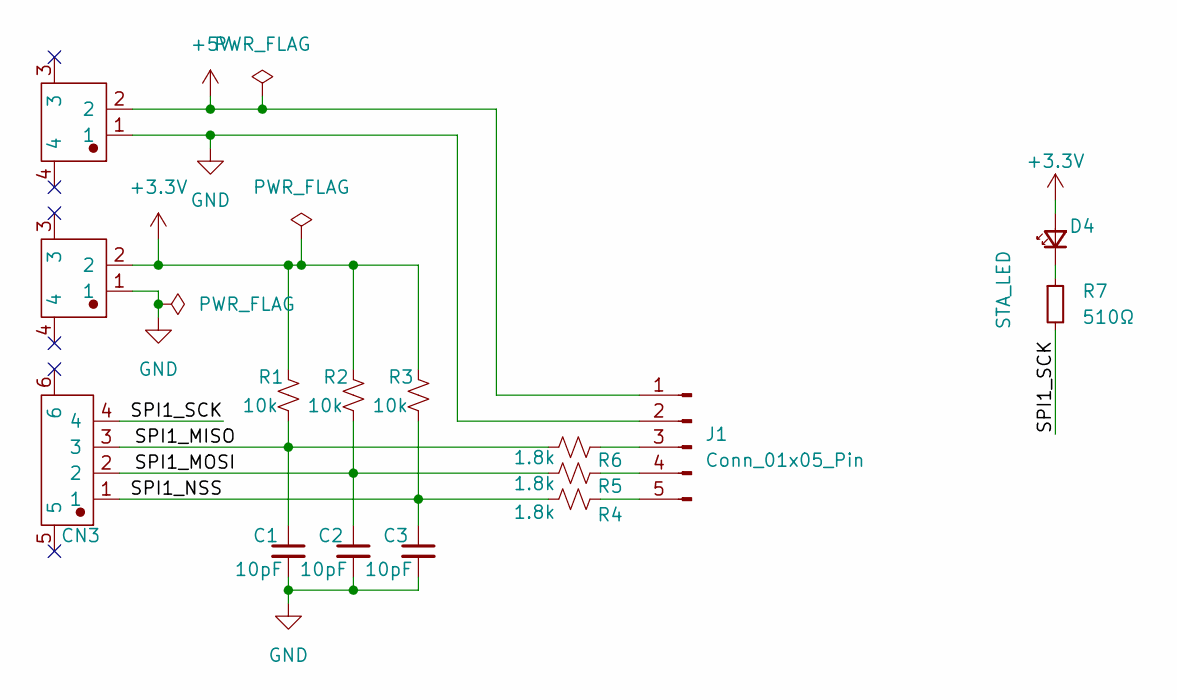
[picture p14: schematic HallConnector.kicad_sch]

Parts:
C1, C2, C3: 10pF; C_0603_1608Metric_Pad1.08x0.95mm_HandSolder
CN3: WAFER-SH1.0-4PWB; CONN-SMD_4P-P1.00_WAFER-SH1.0-4PWB
D4: STA_LED; LED_0603_1608Metric_Pad1.05x0.95mm_HandSolder
J1: Conn_01x05_Pin; PinHeader_1x05_P2.54mm_Vertical
R1, R2, R3: 10k; R_0603_1608Metric_Pad0.98x0.95mm_HandSolder
R4, R5, R6: 1.8k; R_0603_1608Metric_Pad0.98x0.95mm_HandSolder
R7: 510Ω; R_0603_1608Metric_Pad0.98x0.95mm_HandSolder
U1, U2: WAFER-SH1.0-2PWB; CONN-SMD_2P-P1.00_XUNPU_WAFER-SH1.0-2PWB

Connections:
+3.3V: D4.2 (A), R1.1, R2.1, R3.1, U1.2
+5V: J1.1, U2.2
/SPI1_MISO: C1.1, CN3.3, R1.2, R6.1
/SPI1_MOSI: C2.1, CN3.2, R2.2, R5.1
/SPI1_NSS: C3.1, CN3.1, R3.2, R4.1
/SPI1_SCK: CN3.4, R7.2
GND: C1.2, C2.2, C3.2, J1.2, U1.1, U2.1
unnamed: D4.1 (K), R7.1
unnamed: J1.3, R6.2
unnamed: J1.4, R5.2
unnamed: J1.5, R4.2

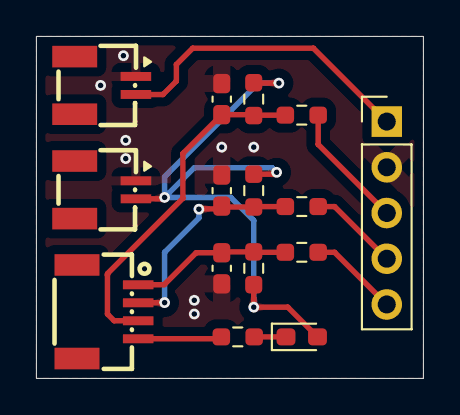
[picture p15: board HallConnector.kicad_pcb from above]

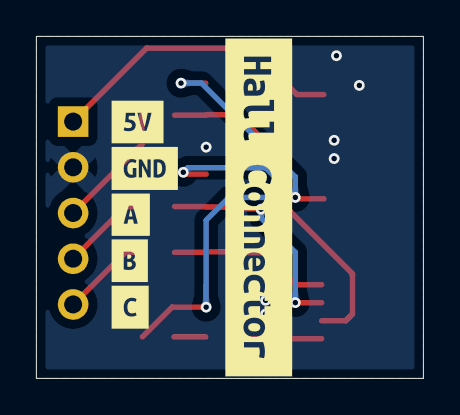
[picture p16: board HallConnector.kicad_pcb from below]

Board: 2 copper layers, 21.5 x 19.0 mm, 21 parts (6 on the bottom side), 11 nets.

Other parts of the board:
kibuzzard-67FE44A7: G***; kibuzzard-67FE44A7
kibuzzard-67FE44AF: G***; kibuzzard-67FE44AF
kibuzzard-67FE44BA: G***; kibuzzard-67FE44BA
kibuzzard-67FE447B: G***; kibuzzard-67FE447B
kibuzzard-67FE4499: G***; kibuzzard-67FE4499
kibuzzard-67FE4510: G***; kibuzzard-67FE4510

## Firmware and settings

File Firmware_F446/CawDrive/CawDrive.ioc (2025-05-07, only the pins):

Mcu.UserName=STM32F446RETx
PA0-WKUP.Signal=ADCx_IN0
PA1.Signal=ADCx_IN1
PA10.Signal=S_TIM1_CH3
PA13.Signal=SYS_JTMS-SWDIO
PA14.Signal=SYS_JTCK-SWCLK
PA15.GPIO_Label=ENCODER_CAL
PA15.Signal=GPIO_Output
PA2.Signal=ADCx_IN2
PA3.Signal=ADCx_IN3
PA5.Signal=GPIO_Output
PA6.Signal=S_TIM3_CH1
PA7.Signal=S_TIM3_CH2
PA8.Signal=S_TIM1_CH1
PA9.Signal=S_TIM1_CH2
PB0.Signal=S_TIM3_CH3
PB1.Signal=ADCx_IN9
PB10.Signal=USART3_TX
PB12.Signal=TIM1_BKIN
PB13.Signal=GPIO_Output
PB14.Signal=GPIO_Output
PB15.Signal=GPIO_Output
PB3.GPIO_Label=ENCODER_SPI_NSS
PB3.Signal=GPIO_Output
PB5.GPIO_Label=CAN_STB
PB5.Signal=GPIO_Output
PB6.Signal=I2C1_SCL
PB7.Signal=I2C1_SDA
PB8.Signal=CAN1_RX
PB9.Signal=CAN1_TX
PC0.Signal=ADCx_IN10
PC1.GPIO_Label=LED_3
PC1.Signal=GPIO_Output
PC10.Signal=SPI3_SCK
PC11.Signal=SPI3_MISO
PC12.Signal=SPI3_MOSI
PC13.Signal=GPIO_Output
PC2.GPIO_Label=LED_2
PC2.Signal=GPIO_Output
PC3.GPIO_Label=LED_1
PC3.Signal=GPIO_Output
PC5.Signal=USART3_RX
PC6.GPIO_Label=TIM1_BREAK
PC6.Signal=GPIO_Output
PC7.GPIO_Label=DRV_CAL
PC7.Signal=GPIO_Output
PC8.GPIO_Label=DRV_ENABLE
PC8.Signal=GPIO_Output
PC9.GPIO_Label=DRV_FAULT
PC9.Signal=GPXTI9
PD2.GPIO_Label=DRV_SPI_NSS
PD2.Signal=GPIO_Output
PH0-OSC_IN.Signal=RCC_OSC_IN
PH1-OSC_OUT.Signal=RCC_OSC_OUT

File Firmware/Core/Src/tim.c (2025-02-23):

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
/* Includes ------------------------------------------------------------------*/
#include "tim.h"

TIM_HandleTypeDef htim1;
TIM_HandleTypeDef htim8;

/* TIM1 init function */
void MX_TIM1_Init(void)
{

  TIM_ClockConfigTypeDef sClockSourceConfig = {0};
  TIM_MasterConfigTypeDef sMasterConfig = {0};
  TIMEx_BreakInputConfigTypeDef sBreakInputConfig = {0};
  TIM_OC_InitTypeDef sConfigOC = {0};
  TIM_BreakDeadTimeConfigTypeDef sBreakDeadTimeConfig = {0};

  htim1.Instance = TIM1;
  htim1.Init.Prescaler = PWM_PRSC;
  htim1.Init.CounterMode = TIM_COUNTERMODE_CENTERALIGNED1;
  htim1.Init.Period = 4000;
  htim1.Init.ClockDivision = TIM_CLOCKDIVISION_DIV1;
  htim1.Init.RepetitionCounter = 1;
  htim1.Init.AutoReloadPreload = TIM_AUTORELOAD_PRELOAD_ENABLE;
  if (HAL_TIM_Base_Init(&htim1) != HAL_OK)
  {
    Error_Handler();
  }
  sClockSourceConfig.ClockSource = TIM_CLOCKSOURCE_INTERNAL;
  if (HAL_TIM_ConfigClockSource(&htim1, &sClockSourceConfig) != HAL_OK)
  {
    Error_Handler();
  }
  if (HAL_TIM_PWM_Init(&htim1) != HAL_OK)
  {
    Error_Handler();
  }
  sMasterConfig.MasterOutputTrigger = TIM_TRGO_RESET;
  sMasterConfig.MasterOutputTrigger2 = TIM_TRGO2_RESET;
  sMasterConfig.MasterSlaveMode = TIM_MASTERSLAVEMODE_DISABLE;
  if (HAL_TIMEx_MasterConfigSynchronization(&htim1, &sMasterConfig) != HAL_OK)
  {
    Error_Handler();
  }
  sBreakInputConfig.Source = TIM_BREAKINPUTSOURCE_BKIN;
  sBreakInputConfig.Enable = TIM_BREAKINPUTSOURCE_ENABLE;
  sBreakInputConfig.Polarity = TIM_BREAKINPUTSOURCE_POLARITY_HIGH;
  if (HAL_TIMEx_ConfigBreakInput(&htim1, TIM_BREAKINPUT_BRK, &sBreakInputConfig) != HAL_OK)
  {
    Error_Handler();
  }
  sConfigOC.OCMode = TIM_OCMODE_PWM1;
  sConfigOC.Pulse = 0;
  sConfigOC.OCPolarity = TIM_OCPOLARITY_HIGH;
  sConfigOC.OCNPolarity = TIM_OCNPOLARITY_HIGH;
  sConfigOC.OCFastMode = TIM_OCFAST_DISABLE;
  sConfigOC.OCIdleState = TIM_OCIDLESTATE_RESET;
  sConfigOC.OCNIdleState = TIM_OCNIDLESTATE_RESET;
  if (HAL_TIM_PWM_ConfigChannel(&htim1, &sConfigOC, TIM_CHANNEL_1) != HAL_OK)
  {
    Error_Handler();
  }
  if (HAL_TIM_PWM_ConfigChannel(&htim1, &sConfigOC, TIM_CHANNEL_2) != HAL_OK)
  {
    Error_Handler();
  }
  if (HAL_TIM_PWM_ConfigChannel(&htim1, &sConfigOC, TIM_CHANNEL_3) != HAL_OK)
  {
    Error_Handler();
  }
  sConfigOC.Pulse = 1500;
  if (HAL_TIM_PWM_ConfigChannel(&htim1, &sConfigOC, TIM_CHANNEL_4) != HAL_OK)
  {
    Error_Handler();
  }
  sBreakDeadTimeConfig.OffStateRunMode = TIM_OSSR_DISABLE;
  sBreakDeadTimeConfig.OffStateIDLEMode = TIM_OSSI_DISABLE;
  sBreakDeadTimeConfig.LockLevel = TIM_LOCKLEVEL_1;
  sBreakDeadTimeConfig.DeadTime = 0;
  sBreakDeadTimeConfig.BreakState = TIM_BREAK_ENABLE;
  sBreakDeadTimeConfig.BreakPolarity = TIM_BREAKPOLARITY_HIGH;
  sBreakDeadTimeConfig.BreakFilter = 0;
  sBreakDeadTimeConfig.BreakAFMode = TIM_BREAK_AFMODE_INPUT;
  sBreakDeadTimeConfig.Break2State = TIM_BREAK2_DISABLE;
  sBreakDeadTimeConfig.Break2Polarity = TIM_BREAK2POLARITY_HIGH;
  sBreakDeadTimeConfig.Break2Filter = 0;
  sBreakDeadTimeConfig.Break2AFMode = TIM_BREAK_AFMODE_INPUT;
  sBreakDeadTimeConfig.AutomaticOutput = TIM_AUTOMATICOUTPUT_DISABLE;
  if (HAL_TIMEx_ConfigBreakDeadTime(&htim1, &sBreakDeadTimeConfig) != HAL_OK)
  {
    Error_Handler();
  }
  HAL_TIM_MspPostInit(&htim1);

}
/* TIM8 init function */
void MX_TIM8_Init(void)
{

  TIM_ClockConfigTypeDef sClockSourceConfig = {0};
  TIM_MasterConfigTypeDef sMasterConfig = {0};

  htim8.Instance = TIM8;
  htim8.Init.Prescaler = PWM_PRSC;
  htim8.Init.CounterMode = TIM_COUNTERMODE_CENTERALIGNED1;
  htim8.Init.Period = 4000;
  htim8.Init.ClockDivision = TIM_CLOCKDIVISION_DIV1;
  htim8.Init.RepetitionCounter = 1;
  htim8.Init.AutoReloadPreload = TIM_AUTORELOAD_PRELOAD_ENABLE;
  if (HAL_TIM_Base_Init(&htim8) != HAL_OK)
  {
    Error_Handler();
  }
  sClockSourceConfig.ClockSource = TIM_CLOCKSOURCE_INTERNAL;
  if (HAL_TIM_ConfigClockSource(&htim8, &sClockSourceConfig) != HAL_OK)
  {
    Error_Handler();
  }
  sMasterConfig.MasterOutputTrigger = TIM_TRGO_RESET;
  sMasterConfig.MasterOutputTrigger2 = TIM_TRGO2_RESET;
  sMasterConfig.MasterSlaveMode = TIM_MASTERSLAVEMODE_DISABLE;
  if (HAL_TIMEx_MasterConfigSynchronization(&htim8, &sMasterConfig) != HAL_OK)
  {
    Error_Handler();
  }
}

void HAL_TIM_Base_MspInit(TIM_HandleTypeDef* tim_baseHandle)
{

  GPIO_InitTypeDef GPIO_InitStruct = {0};
  if(tim_baseHandle->Instance==TIM1)
  {
    /* TIM1 clock enable */
    __HAL_RCC_TIM1_CLK_ENABLE();

    __HAL_RCC_GPIOB_CLK_ENABLE();
    /**TIM1 GPIO Configuration
    PB12     ------> TIM1_BKIN
    */
    GPIO_InitStruct.Pin = GPIO_PIN_12;
    GPIO_InitStruct.Mode = GPIO_MODE_AF_OD;
    GPIO_InitStruct.Pull = GPIO_NOPULL;
    GPIO_InitStruct.Speed = GPIO_SPEED_FREQ_LOW;
    GPIO_InitStruct.Alternate = GPIO_AF6_TIM1;
    HAL_GPIO_Init(GPIOB, &GPIO_InitStruct);

    /* TIM1 interrupt Init */
    HAL_NVIC_SetPriority(TIM1_UP_TIM16_IRQn, 10, 0);
    HAL_NVIC_EnableIRQ(TIM1_UP_TIM16_IRQn);
  }
  else if(tim_baseHandle->Instance==TIM8)
  {
    /* TIM8 clock enable */
    __HAL_RCC_TIM8_CLK_ENABLE();

    /* TIM8 interrupt Init */
    HAL_NVIC_SetPriority(TIM8_UP_IRQn, 5, 0);
    HAL_NVIC_EnableIRQ(TIM8_UP_IRQn);
  }
}
void HAL_TIM_MspPostInit(TIM_HandleTypeDef* timHandle)
{

  GPIO_InitTypeDef GPIO_InitStruct = {0};
  if(timHandle->Instance==TIM1)
  {
    __HAL_RCC_GPIOA_CLK_ENABLE();
    /**TIM1 GPIO Configuration
    PA8     ------> TIM1_CH1
    PA9     ------> TIM1_CH2
    PA10     ------> TIM1_CH3
    */
    GPIO_InitStruct.Pin = GPIO_PIN_8|GPIO_PIN_9|GPIO_PIN_10;
    GPIO_InitStruct.Mode = GPIO_MODE_AF_PP;
    GPIO_InitStruct.Pull = GPIO_NOPULL;
    GPIO_InitStruct.Speed = GPIO_SPEED_FREQ_LOW;
    GPIO_InitStruct.Alternate = GPIO_AF6_TIM1;
    HAL_GPIO_Init(GPIOA, &GPIO_InitStruct);

  }

}

void HAL_TIM_Base_MspDeInit(TIM_HandleTypeDef* tim_baseHandle)
{

  if(tim_baseHandle->Instance==TIM1)
  {
    /* Peripheral clock disable */
    __HAL_RCC_TIM1_CLK_DISABLE();

    /**TIM1 GPIO Configuration
    PB12     ------> TIM1_BKIN
    PA8     ------> TIM1_CH1
    PA9     ------> TIM1_CH2
    PA10     ------> TIM1_CH3
    */
    HAL_GPIO_DeInit(GPIOB, GPIO_PIN_12);

    HAL_GPIO_DeInit(GPIOA, GPIO_PIN_8|GPIO_PIN_9|GPIO_PIN_10);

    /* TIM1 interrupt Deinit */
    HAL_NVIC_DisableIRQ(TIM1_UP_TIM16_IRQn);
  }
  else if(tim_baseHandle->Instance==TIM8)
  {
    /* Peripheral clock disable */
    __HAL_RCC_TIM8_CLK_DISABLE();

    /* TIM8 interrupt Deinit */
    HAL_NVIC_DisableIRQ(TIM8_UP_IRQn);
  }
}



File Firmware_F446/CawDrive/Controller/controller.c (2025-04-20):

#include "./controller.h"

#include <string.h>

#include "./Devices/dev_usart.h"
#include "./Drivers/drv8323/drv8323.h"
#include "./FOC/VF.h"
#include "./PWM/pwm.h"
#include "./Sensors/current.h"
#include "./Sensors/hall.h"
#include "./State/state.h"
#include "./temp.h"
#include "./vbus.h"

drv8323_t g_driver;

float load_data[5];
static uint8_t g_tmp[24] = {0, 0, 0, 0, 0, 0, 0, 0, 0, 0, 0,    0,
                            0, 0, 0, 0, 0, 0, 0, 0, 0, 0, 0x80, 0x7f};

void controller_init(void) {
  /// 初始化串口
  dev_usart_init();

  /// 配置DRV8323

  // 使用PWM_MODE_3X控制时将互补引脚拉低
  HAL_GPIO_WritePin(GPIOB, GPIO_PIN_13, GPIO_PIN_SET);
  HAL_GPIO_WritePin(GPIOB, GPIO_PIN_14, GPIO_PIN_SET);
  HAL_GPIO_WritePin(GPIOB, GPIO_PIN_15, GPIO_PIN_SET);

  drv8323_init(&g_driver, &hspi3);
  drv8323_calibrate(&g_driver);
  HAL_Delay(10);
  drv8323_write_dcr(&g_driver, 0x0, DIS_GDF_DIS, 0x0, PWM_MODE_3X, 0x0, 0x0,
                    0x0, 0x0, 0x1);
  HAL_Delay(10);
  drv8323_write_csacr(&g_driver, 0x0, 0x1, 0x0, CSA_GAIN_40, 0x0, 0x1, 0x1, 0x1,
                      SEN_LVL_1_0);
  HAL_Delay(10);
  drv8323_write_csacr(&g_driver, 0x0, 0x1, 0x0, CSA_GAIN_40, 0x1, 0x0, 0x0, 0x0,
                      SEN_LVL_1_0);
  HAL_Delay(10);
  drv8323_write_ocpcr(&g_driver, TRETRY_50US, DEADTIME_50NS, OCP_NONE,
                      OCP_DEG_8US, VDS_LVL_1_88);
  drv8323_enable_gd(&g_driver);

  HAL_Delay(10);

  // rtU.SpeedRef = 800;

  rtU.Vbus = vbus_get();

  current_init();
  vbus_init();
  hall_init();
  pwm_init();

  // rtU.Motor_OnOff = 1;

  rtU.ud = 0;
  rtU.uq = 12;
  rtU.Freq = 4;

  pwm_start();

  state_set(STATE_RUN);
}

void controller_step(void) {
  // float temp = temp_get();
  rtU.Vbus = vbus_get();
}

void core_callback() {
  // hall_step();
  // rtU.theta = hall_get_theta();
  // rtU.SpeedFd = hall_get_speed();

  float current[3];

  current_get(current);

  // rtU.ia = current[0];
  // rtU.ib = current[1];
  // rtU.ic = current[2];
  VF_step();

  TIM1->CCR1 = rtY.tABC[0];
  TIM1->CCR2 = rtY.tABC[1];
  TIM1->CCR3 = rtY.tABC[2];

  load_data[0] = current[0];
  load_data[1] = current[1];
  load_data[2] = current[2];
  load_data[3] = rtY.tABC[0];
  load_data[4] = rtY.tABC[1];
  memcpy(g_tmp, (uint8_t *)load_data, sizeof(load_data));

  dev_usart_write(g_tmp, sizeof(g_tmp));
}

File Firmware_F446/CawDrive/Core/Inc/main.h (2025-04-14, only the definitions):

#define LED_3_Pin GPIO_PIN_1
#define LED_3_GPIO_Port GPIOC
#define LED_2_Pin GPIO_PIN_2
#define LED_2_GPIO_Port GPIOC
#define LED_1_Pin GPIO_PIN_3
#define LED_1_GPIO_Port GPIOC
#define TIM1_BREAK_Pin GPIO_PIN_6
#define TIM1_BREAK_GPIO_Port GPIOC
#define DRV_CAL_Pin GPIO_PIN_7
#define DRV_CAL_GPIO_Port GPIOC
#define DRV_ENABLE_Pin GPIO_PIN_8
#define DRV_ENABLE_GPIO_Port GPIOC
#define DRV_FAULT_Pin GPIO_PIN_9
#define DRV_FAULT_GPIO_Port GPIOC
#define ENCODER_CAL_Pin GPIO_PIN_15
#define ENCODER_CAL_GPIO_Port GPIOA
#define DRV_SPI_NSS_Pin GPIO_PIN_2
#define DRV_SPI_NSS_GPIO_Port GPIOD
#define ENCODER_SPI_NSS_Pin GPIO_PIN_3
#define ENCODER_SPI_NSS_GPIO_Port GPIOB
#define CAN_STB_Pin GPIO_PIN_5
#define CAN_STB_GPIO_Port GPIOB

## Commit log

2023-08-26 🎉初始提交
    [CawDrive.kicad_pcb, CawDrive.kicad_sch, DRV8323RSRGZR.kicad_sch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]
2023-09-17 参考MIT驱动器进行改版
    [CawDrive.kicad_pcb, CawDrive.kicad_sch, DRV8323RSRGZR.kicad_sch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]
2023-09-19 将线性稳压芯片和CAN芯片替换成TI的相关型号
    [CawDrive.kicad_pcb, CawDrive.kicad_sch, DRV8323RSRGZR.kicad_sch]
2023-09-19 拼板制作
    [CawDrive.kicad_pcb]
2023-10-02 优化底层丝印
    [CawDrive.kicad_pcb]
2023-10-03 优化布线
    [CawDrive.kicad_pcb, CawDrive.kicad_sch, DRV8323RSRGZR.kicad_sch]
2023-10-04 更新README
2023-10-04 添加Gerber文件
    [CawDrive-B_Cu.gbr, CawDrive-B_Mask.gbr, CawDrive-B_Paste.gbr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]
2023-10-04 生成BOM物料表
    [CawDrive.kicad_pcb]
2023-10-04 更新BOM
    [CawDrive.csv]
2024-08-23 升级主控STM32G474，增加AS5047P编码器，支持NTC温度采样
    [CawDrive-B_Cu.gbr, CawDrive-B_Mask.gbr, CawDrive-B_Paste.gbr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]
2024-09-25 合并固件代码
    [CawDrive-B_Cu.gbr, CawDrive-B_Mask.gbr, CawDrive-B_Paste.gbr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]
2024-09-27 支持AS5047P传感器读取位置信息
2024-09-28 完善编码器功能，将编码器对象添加到Motor
2024-09-30 完成闭环速度控制🥳
2024-10-01 完成闭环位置控制
2024-11-14 完成电流闭环控制
2025-02-12 新增电机初始化功能，支持参数存储Flash
2025-02-15 优化串口数据传输
2025-02-15 新增参数存储功能
2025-02-23 优化通讯和事件处理
2025-04-05 升级V2版，支持3路电流采样以及霍尔传感器
    [CawDrive.kicad_pcb, CawDrive.kicad_sch, DRV8323RSRGZR.kicad_sch]
2025-04-05 增加测试点PC13引脚
    [CawDrive.kicad_pcb, CawDrive.kicad_sch]
2025-04-07 更新文档
    [CawDrive.kicad_pcb]
2025-04-07 删除caw_embedded链接
2025-04-07 优化布线，生成Gerber文件
    [CawDrive-B_Cu.gbr, CawDrive-B_Mask.gbr, CawDrive-B_Paste.gbr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]
2025-04-08 增加HALL传感器接口板
    [CawDrive-B_Cu.gbr, CawDrive-B_Mask.gbr, CawDrive-B_Paste.gbr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]
2025-04-10 更新电阻精度，重新生成BOM
    [CawDrive.csv, CawDrive.kicad_sch, HallConnector.csv]
2025-04-13 更新采样电阻精度，重新生成BOM
    [CawDrive.csv, CawDrive.kicad_pcb, CawDrive.kicad_sch]
2025-04-14 测试PWM波形，完成状态LED控制
2025-04-15 修复霍尔接口板线序问题，完成串口测试
    [HallConnector-B_Cu.gbr, HallConnector-B_Mask.gbr, HallConnector-B_Paste.gbr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]
2025-04-15 完成低端电流采样触发时间测试
    [HallConnector-B_Cu.gbr, HallConnector-B_Mask.gbr, HallConnector-B_Paste.gbr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]
2025-04-16 完成三相电流采样与母线电压采样
2025-04-17 完成驱动器温度采样
2025-04-18 测试霍尔编码器数据读取，完善README
2025-04-20 优化电流采样布线
    [CawDrive.kicad_pcb]
2025-04-21 优化ADC采样布线
    [CawDrive.kicad_pcb, CawDrive.kicad_sch, DRV8323RSRGZR.kicad_sch]
2025-04-21 优化走线
    [CawDrive.kicad_pcb]
2025-04-22 更新Gerber
    [CawDrive-B_Cu.gbr, CawDrive-B_Mask.gbr, CawDrive-B_Paste.gbr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]
2025-04-23 PCB走线优化
    [CawDrive.kicad_pcb]
2025-04-23 文档更新
    [CawDrive-B_Cu.gbr, CawDrive-B_Mask.gbr, CawDrive-B_Paste.gbr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]
2025-05-07 优化PCB
    [CawDrive-B_Cu.gbr, CawDrive-B_Mask.gbr, CawDrive-B_Paste.gbr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]

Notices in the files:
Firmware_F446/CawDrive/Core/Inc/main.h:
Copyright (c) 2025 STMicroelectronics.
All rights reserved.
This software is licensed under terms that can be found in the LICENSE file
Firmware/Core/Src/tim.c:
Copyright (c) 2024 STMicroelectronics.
